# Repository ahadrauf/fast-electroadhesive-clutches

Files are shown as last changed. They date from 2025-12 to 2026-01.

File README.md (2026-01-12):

# Optimizing Electroadhesive Clutches for Sub-Millisecond Response Times

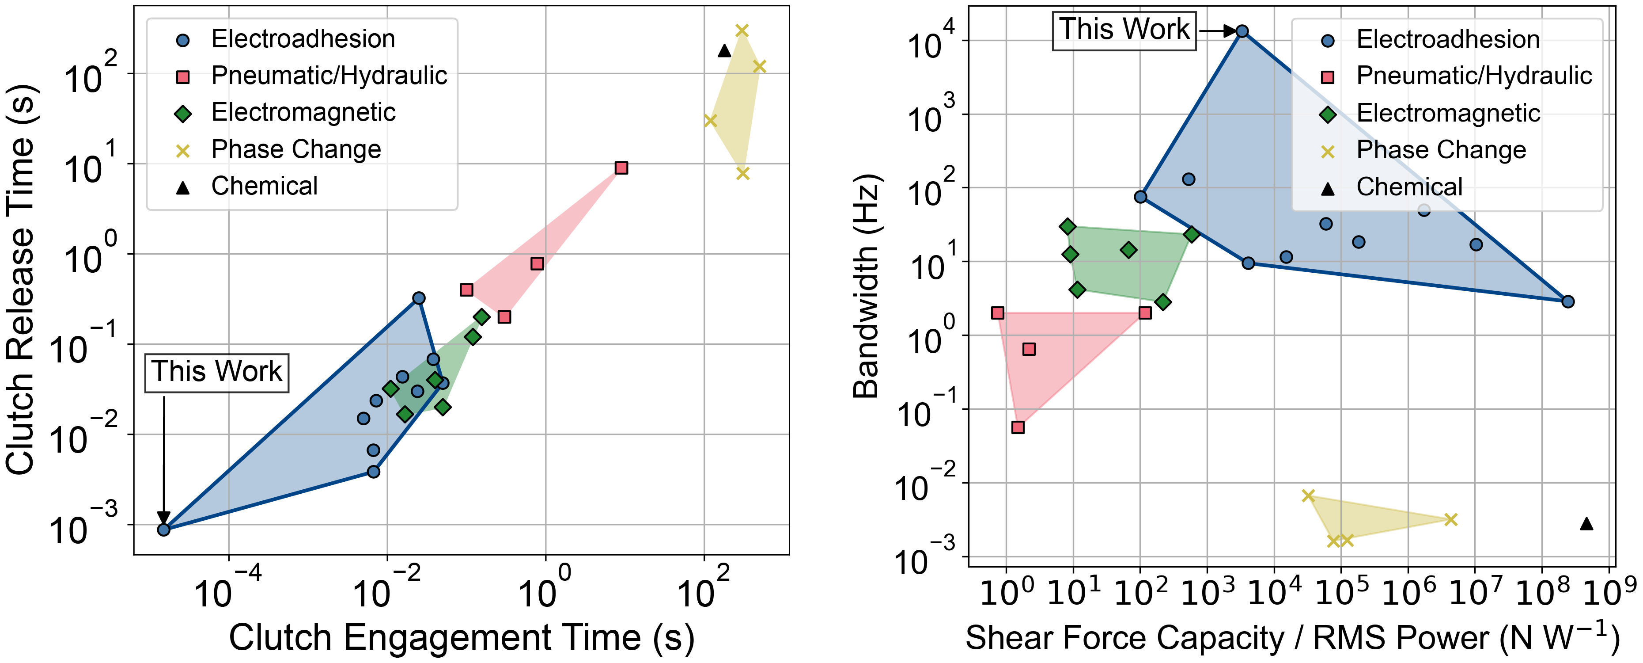
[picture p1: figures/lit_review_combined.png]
This study presents fast, electrically controllable electroadhesive clutches that offer over 10x faster engagement, release, and dynamic bandwidth compared to prior work and other clutch technologies.


Robots can use fast, controllable clutches for dynamic load bearing and programmable stiffness. Electroadhesion (EA) is a technology that offers these capabilities in an ultra-compact and flexible form factor, but its inconsistent dynamics limit real-world use.

To address this uncertainty, we built an analytical electromechanical dynamics model for electroadhesion, factoring in contact mechanics between the dielectric and substrate, polarization dynamics, and the drive circuitry’s rise and fall times. Dual optimization over both the electrical and contact mechanics allows us to improve clutch dynamics while maintaining high force output. The fastest clutches in our study can repeatably:
 * Engage in <15 μs (10x faster than prior work)
 * Release in <1 ms (17x faster than prior work)
 * Bandwidth >10 kHz (10x higher than prior work)
 * Recover after slip in <4 ms (roughly 5x faster than prior work)

In the main paper (open access link [here](https://arxiv.org/abs/2412.16803), journal link [here](https://www.sciencedirect.com/science/article/abs/pii/S235243162500094X)), we compare our model’s predictions for electroadhesive engagement and release times to experimental results across four operating and geometric design parameters with good conformity. We find that higher drive frequencies and narrower substrate aspect ratios enable significantly faster actuator response times, in particular improving release times.

We also compare our model’s predictions to broader experimental trends in prior literature, in particular explaining why larger substrate widths and lengths, lower voltages, and intermediate dielectric thicknesses result in larger release times. To our knowledge, this is the first analytical model for electroadhesion explaining these experimental trends.

## Methods (Modeling)
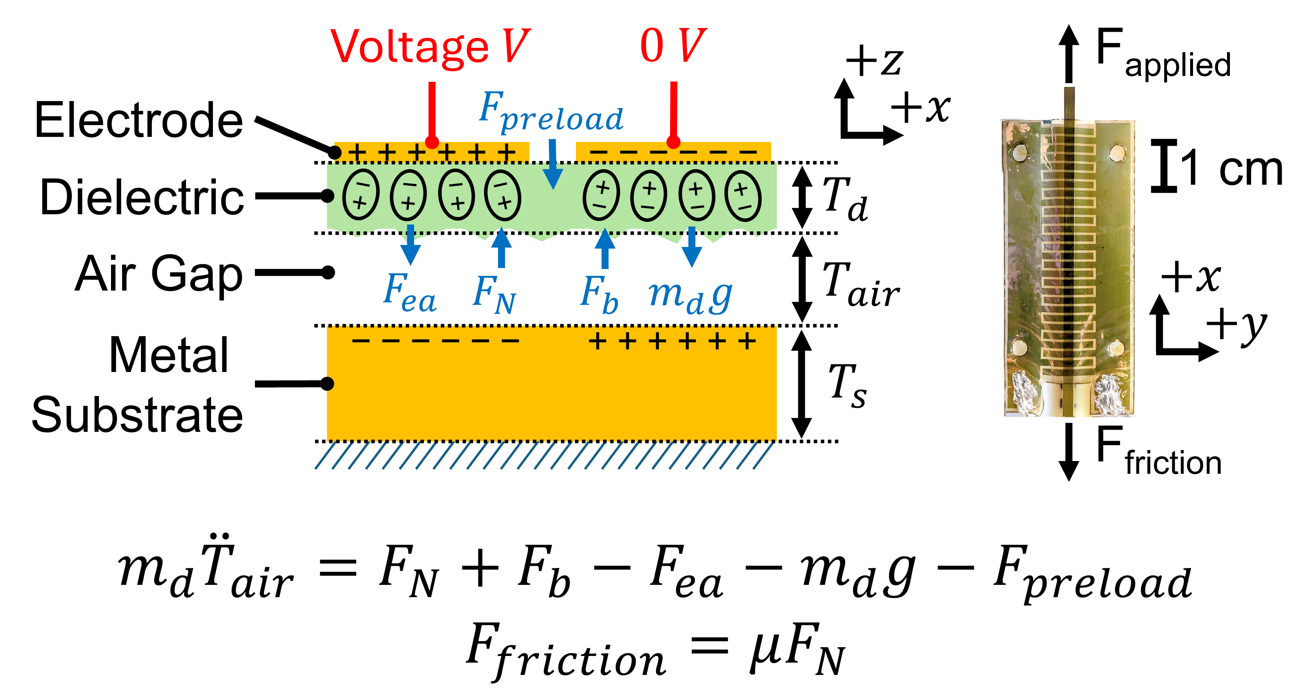
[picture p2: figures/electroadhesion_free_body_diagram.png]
Free body diagram and visualization of an electroadhesive clutch adhering to a metal substrate

Our analytical model for electroadhesion dynamics included, from left to right in the equation above, the contact mechanics force between the dielectric and substrate, squeeze film damping, the electroadhesive attractive force, the dielectric's weight, and any external applied loads.

Using our free body diagram, we simulated how these parameters affect electroadhesion’s quasistatic and dynamic performance, and we validated these simulations via both finite element analysis and experimental testing.  

## Methods (Experimental)
To measure the engagement and release times of electroadhesive clutches down to the tens of microseconds, we built a custom tensile testing setup, as shown below.

We also designed a custom high voltage DC-DC converter and shift register circuit, the schematic of which is shown below.

Experimental test setup for measuring EA shear force as the load cell on a motorized stage pushes against the substrate.

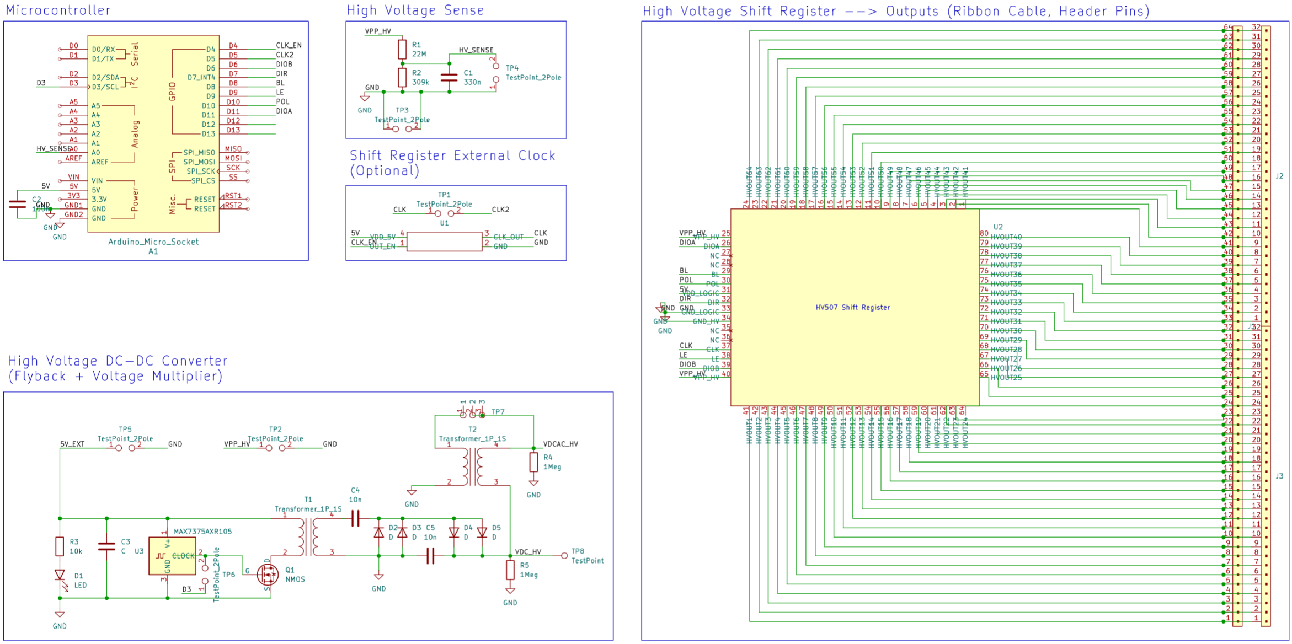
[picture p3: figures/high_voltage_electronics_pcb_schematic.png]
Schematic for the high voltage electronics, featuring a flyback transformer and voltage multiplier to produce the high voltage and a 64-channel shift register to control the electroadhesive clutch.


## Navigating This Repository
Each of the figures in the ``scripts/`` folder are named according to the paper figure they generate. The experimental data that produced these figures are stored in the ``data/`` folder (mostly comprising log files for the ~400 tensile testing experiments reported on in this paper).

The code to run a tensile test is located in ``scripts/run_tensile_test.py``. This script expects that the code in the ``teensy/`` folder has also been loaded onto both the Teensy microcontrollers controlling the tensile testing setup and the shift register PCB.

CAD files for the tensile testing setup are located in the ``cad/`` folder, and KiCAD PCB files for the Microchip HV 507 shift register and power electronics circuit are located in the ``pcb/`` folder.

## Bibliography
[1] A. M. Rauf and S. Follmer, “Modeling the dynamics of sub-millisecond electroadhesive engagement and release times,” Extreme Mechanics Letters, vol. 79, p. 102382, Sept. 2025, doi: [10.1016/j.eml.2025.102382](https://doi.org/10.1016/j.eml.2025.102382). (Open Access arXiv link [here](https://arxiv.org/abs/2412.16803))

@article{Rauf_Follmer_2025, title={Modeling the dynamics of sub-millisecond electroadhesive engagement and release times}, volume={79}, rights={All rights reserved}, ISSN={2352-4316}, DOI={10.1016/j.eml.2025.102382}, abstractNote={Electroadhesive clutches are electrically controllable switchable adhesives commonly used in soft robots and haptic user interfaces. They can form strong bonds to a wide variety of surfaces at low power consumption. However, electroadhesive clutches in the literature engage to and release from substrates several orders of magnitude slower than a traditional electrostatic model would predict. Large release times, in particular, can limit electroadhesion’s usefulness in high-bandwidth applications. We develop a novel electromechanical model for electroadhesion, factoring in polarization dynamics, the drive circuitry’s rise and fall times, and contact mechanics between the dielectric and substrate. We show in simulation and experimentally how different design parameters affect the engagement and release times of centimeter-scale electroadhesive clutches to metallic substrates, and we find that the model accurately captures the magnitude and trends of our experimental results. In particular, we find that higher drive frequencies, narrower substrate aspect ratios, and faster drive circuitry output stages enable significantly faster release times. The fastest clutches have engagement times less than 15μs and release times less than 875μs, which are 10× and 17.1× faster, respectively, than the best times found in prior literature on centimeter-scale electroadhesive clutches.}, journal={Extreme Mechanics Letters}, author={Rauf, Ahad M. and Follmer, Sean}, year={2025}, month=sept, pages={102382} }

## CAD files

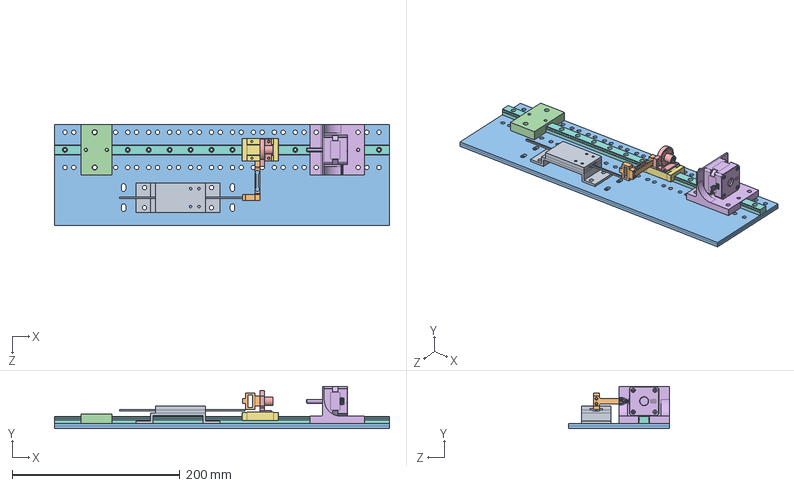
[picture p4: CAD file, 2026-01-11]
cad/tensile_testing_setup.SLDASM
400.0 x 50.3 x 120.0 mm
Linear Guide Rail LML9B
Linear Guide Block LML9B
20240705_msd_bts_nema14_mount
20240705_msd_bts_leadscrew_linearslide_adapter
20240705_msd_bts_leadscrew_fixedbearing_mount
20240705_msd_bts_baseplate
20240705_500g_load_cell
20240706_msd_bts_ea_brake_mount_40mm

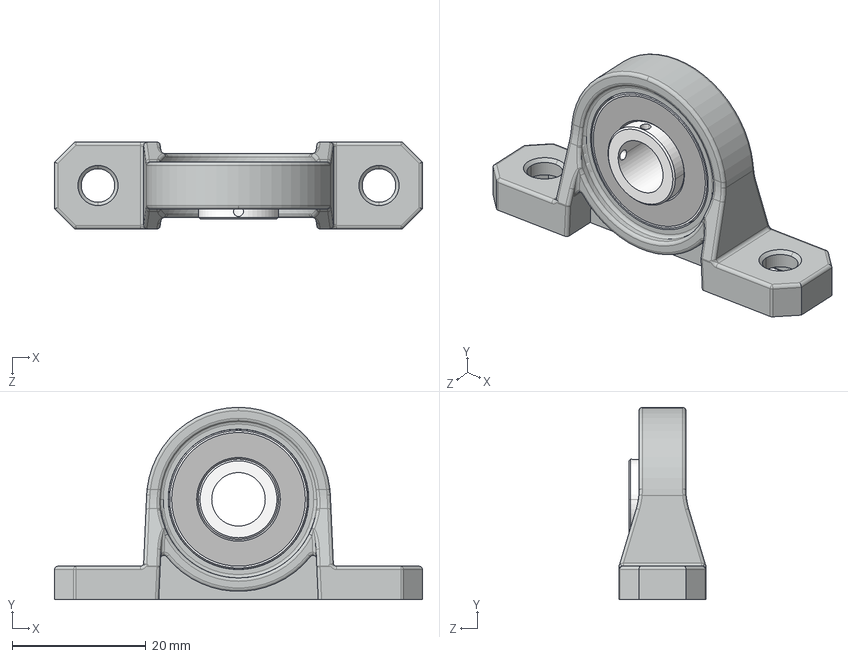
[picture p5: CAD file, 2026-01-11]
cad/pillow_block_8mm.STEP
55.0 x 28.8 x 13.0 mm

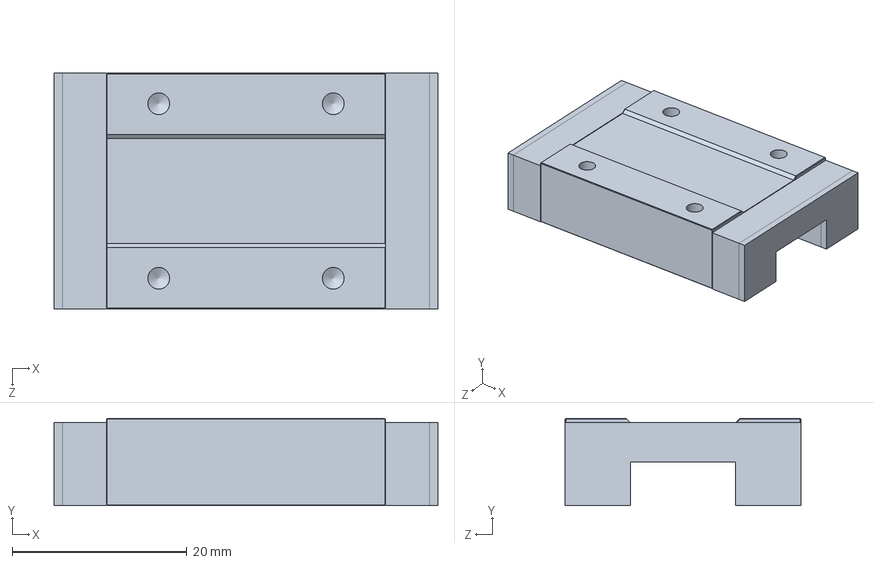
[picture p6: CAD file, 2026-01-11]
cad/Linear Guide Block LML9B.SLDPRT
44.0 x 10.0 x 27.0 mm

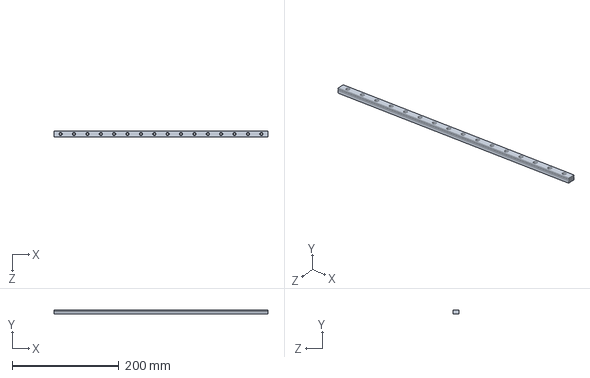
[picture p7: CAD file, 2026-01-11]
cad/Linear Guide Rail LML9B.SLDPRT
400.0 x 8.00 x 12.0 mm

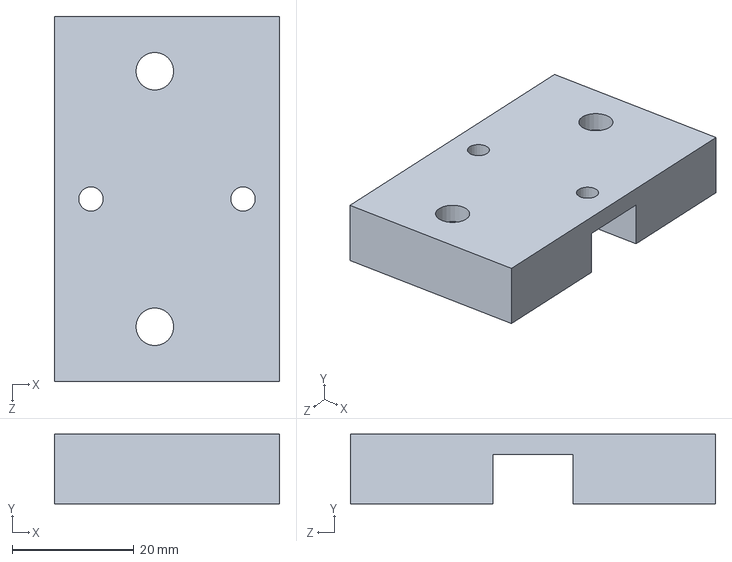
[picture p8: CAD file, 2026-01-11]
cad/20240705_msd_bts_leadscrew_fixedbearing_mount.SLDPRT
37.0 x 11.5 x 60.0 mm

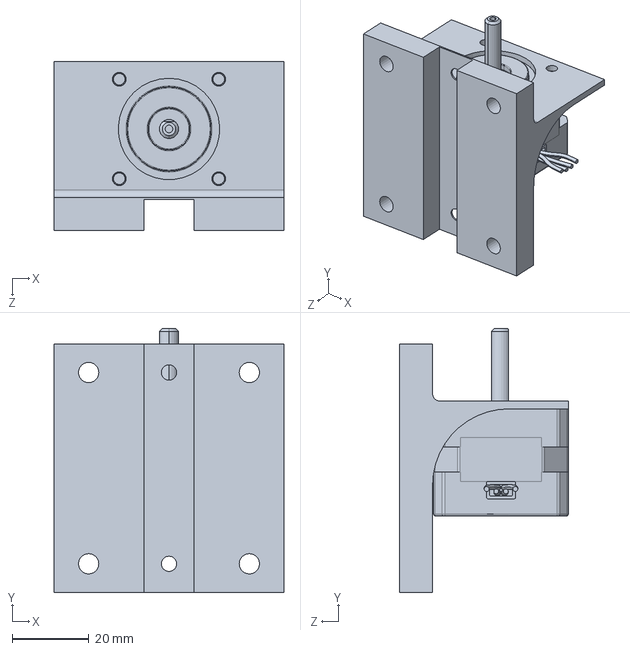
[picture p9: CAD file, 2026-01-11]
cad/20240705_msd_bts_nema14_mount.SLDPRT
60.0 x 69.0 x 44.1 mm

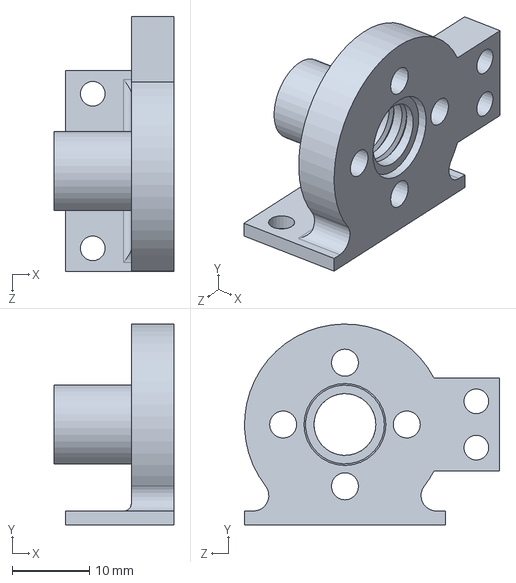
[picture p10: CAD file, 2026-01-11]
cad/20240705_msd_bts_leadscrew_linearslide_adapter.SLDPRT
15.5 x 26.0 x 33.0 mm

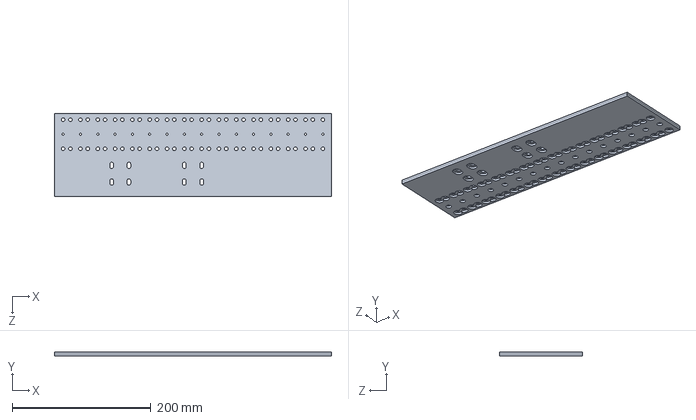
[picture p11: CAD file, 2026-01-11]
cad/20240705_msd_bts_baseplate.SLDPRT
400.0 x 6.16 x 120.0 mm

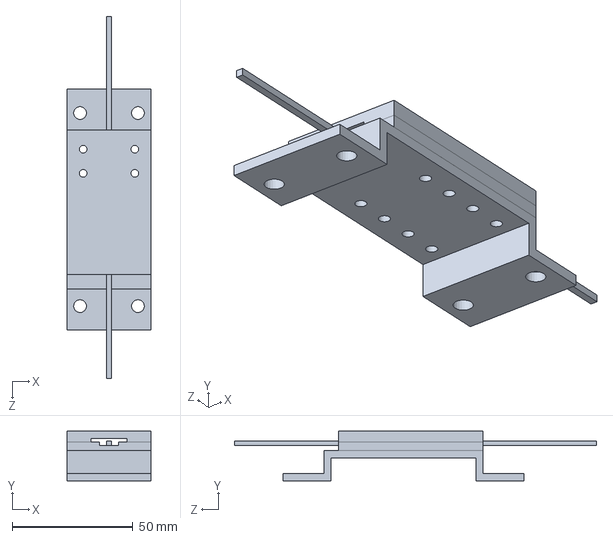
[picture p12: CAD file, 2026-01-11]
cad/20240706_msd_bts_ea_brake_mount_40mm.SLDPRT
35.0 x 20.7 x 150.0 mm

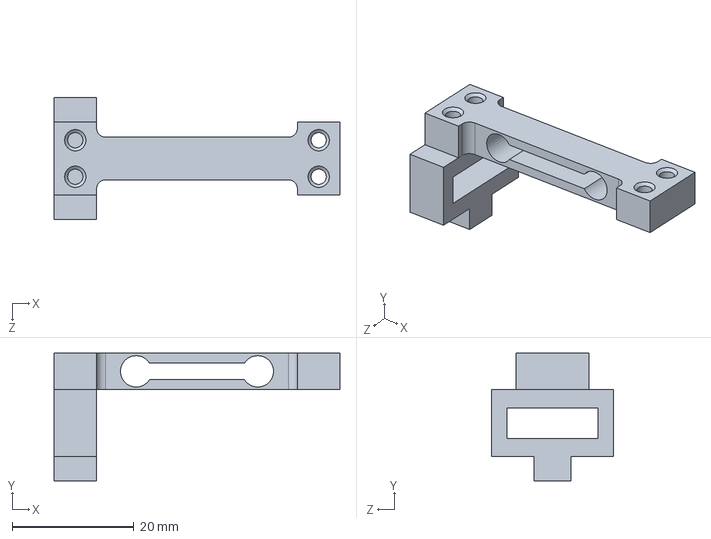
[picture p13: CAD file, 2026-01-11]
cad/20240705_500g_load_cell.SLDPRT
47.0 x 21.0 x 20.0 mm

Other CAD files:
cad/pillow_block_8mm.SLDPRT

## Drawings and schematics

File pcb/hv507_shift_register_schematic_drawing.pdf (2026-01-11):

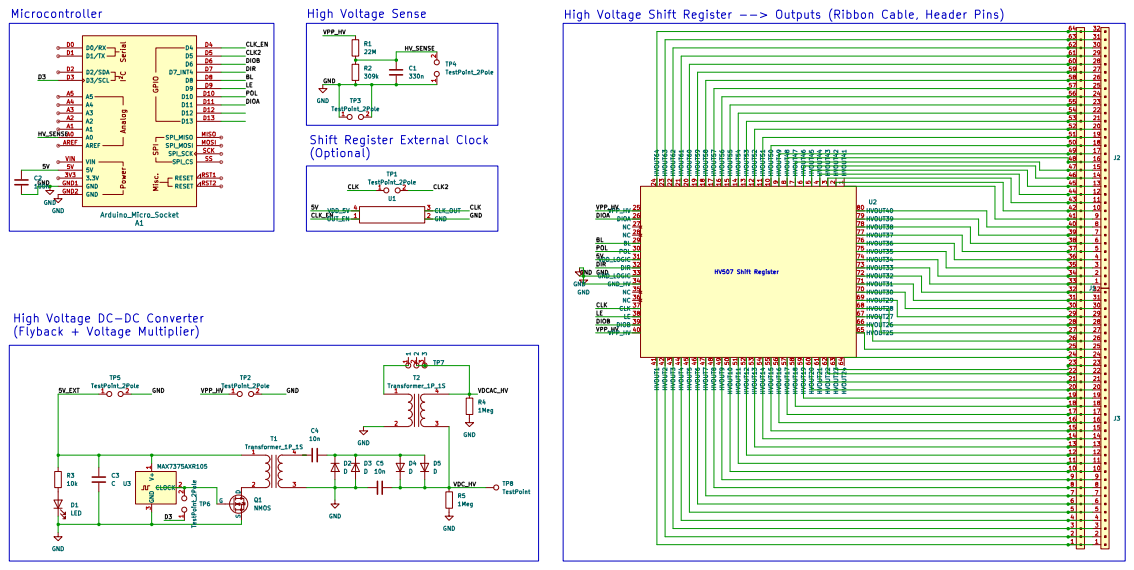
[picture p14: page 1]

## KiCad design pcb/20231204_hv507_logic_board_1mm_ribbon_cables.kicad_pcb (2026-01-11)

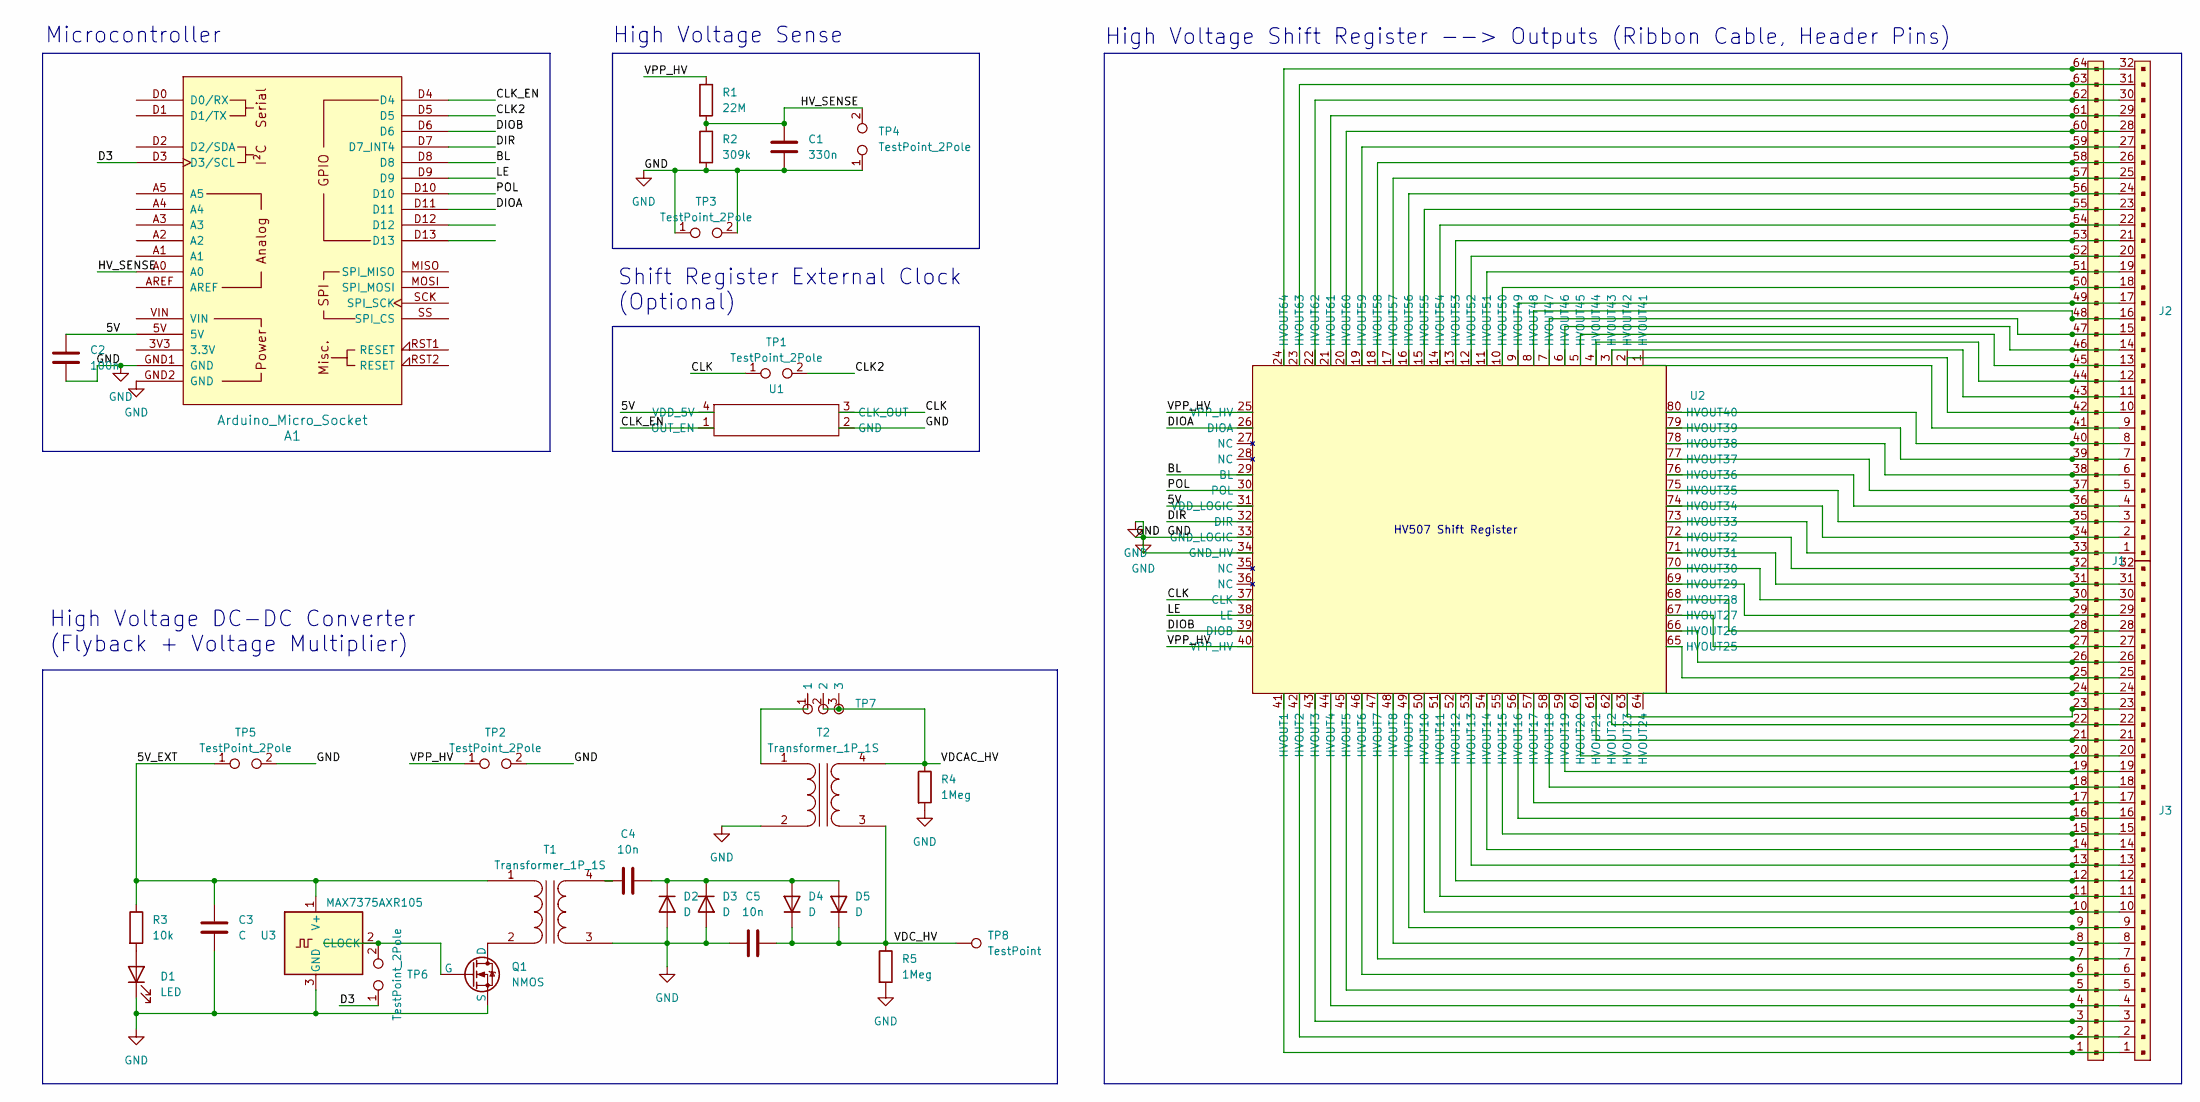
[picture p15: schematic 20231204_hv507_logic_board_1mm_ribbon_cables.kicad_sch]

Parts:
A1: Arduino_Micro_Socket; Arduino_Micro_Socket_ProbeRow
C1: 330n; C_0603_1608Metric_Pad1.08x0.95mm_HandSolder
C2: 100n; C_0603_1608Metric_Pad1.08x0.95mm_HandSolder
C3: C; C_0603_1608Metric_Pad1.08x0.95mm_HandSolder
C4, C5: 10n; C_0603_1608Metric_Pad1.08x0.95mm_HandSolder
D1: LED; C_0603_1608Metric_Pad1.08x0.95mm_HandSolder
D2, D4: D; TO-220-2_Vertical
D3, D5: D; D_SOD-523
J1: PinHeader_32x2_P2.54mm_Vertical2
J2, J3: CF25321D0R0-10-NH
Q1: NMOS; SOT-883
R1: 22M; R_0805_2012Metric_Pad1.20x1.40mm_HandSolder
R2: 309k; R_0805_2012Metric_Pad1.20x1.40mm_HandSolder
R3: 10k; R_0805_2012Metric_Pad1.20x1.40mm_HandSolder
R4, R5: 1Meg; R_0805_2012Metric_Pad1.20x1.40mm_HandSolder
T1: Transformer_1P_1S; UA7868-AE Coupled Inductor
T2: Transformer_1P_1S; LPD5030V 1-1 Coupled Inductor
TP1, TP2, TP3, TP4, TP5, TP6: TestPoint_2Pole; PinHeader_1x02_P2.54mm_Vertical
TP7: PinHeader_1x03_P2.54mm_Vertical
TP8: TestPoint; PinHeader_1x01_P2.54mm_Vertical
U1: SMD-4_3.2x2.5
U2: PQFP-80_14x20mm_P0.8mm
U3: MAX7375AXR105; SOT-323_SC-70

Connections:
/5V: A1.5V, C2.1, U1.4 (VDD_5V), U2.31 (VDD_LOGIC)
/5V_EXT: C3.2, R3.1, T1.1 (AA), TP5.1, U3.1 (V+)
/BL: A1.D8, U2.29 (BL)
/CLK: TP1.1, U1.3 (CLK_OUT), U2.37 (CLK)
/CLK2: A1.D5, TP1.2
/CLK_EN: A1.D4, U1.1 (OUT_EN)
/D3: A1.D3 (D3/SCL), TP6.1
/DIOA: A1.D11, U2.26 (DIOA)
/DIOB: A1.D6, U2.39 (DIOB)
/DIR: A1.D7 (D7_INT4), U2.32 (DIR)
/HV_SENSE: A1.A0, C1.1, R1.2, R2.1, TP4.2
/LE: A1.D9, U2.38 (LE)
/POL: A1.D10, U2.30 (POL)
/VDCAC_HV: R4.1, T2.4 (SB), TP7.2, TP7.3
/VDC_HV: C5.2, D4.1 (K), D5.1 (K), R5.1, T2.3 (SA), TP8.1
/VPP_HV: R1.1, TP2.1, U2.25 (VPP_HV), U2.40 (VPP_HV)
GND: A1.GND1 (GND), A1.GND2 (GND), C1.2, C2.2, C3.1, C5.1, D1.1 (K), D2.2 (A), D3.2 (A), Q1.3 (S), R2.2, R4.2, R5.2, T1.3 (SA), T2.2 (AB), TP2.2, TP3.1, TP3.2, TP4.1, TP5.2, U1.2 (GND), U2.33 (GND_LOGIC), U2.34 (GND_HV), U3.3 (GND)
unnamed: D1.2 (A), R3.2
unnamed: C4.2, D2.1 (K), D3.1 (K), D4.2 (A), D5.2 (A)
unnamed: Q1.1 (D), T1.2 (AB)
unnamed: Q1.2 (G), TP6.2, U3.2 (CLOCK)
unnamed: C4.1, T1.4 (SB)
unnamed: T2.1 (AA), TP7.1
unnamed: J1.1, J3.1, U2.41 (HVOUT1)
unnamed: J1.2, J3.2, U2.42 (HVOUT2)
unnamed: J1.3, J3.3, U2.43 (HVOUT3)
unnamed: J1.4, J3.4, U2.44 (HVOUT4)
unnamed: J1.5, J3.5, U2.45 (HVOUT5)
unnamed: J1.6, J3.6, U2.46 (HVOUT6)
unnamed: J1.7, J3.7, U2.47 (HVOUT7)
unnamed: J1.8, J3.8, U2.48 (HVOUT8)
unnamed: J1.9, J3.9, U2.49 (HVOUT9)
unnamed: J1.10, J3.10, U2.50 (HVOUT10)
unnamed: J1.11, J3.11, U2.51 (HVOUT11)
unnamed: J1.12, J3.12, U2.52 (HVOUT12)
unnamed: J1.13, J3.13, U2.53 (HVOUT13)
unnamed: J1.14, J3.14, U2.54 (HVOUT14)
unnamed: J1.15, J3.15, U2.55 (HVOUT15)
unnamed: J1.16, J3.16, U2.56 (HVOUT16)
unnamed: J1.17, J3.17, U2.57 (HVOUT17)
unnamed: J1.18, J3.18, U2.58 (HVOUT18)
unnamed: J1.19, J3.19, U2.59 (HVOUT19)
unnamed: J1.20, J3.20, U2.60 (HVOUT20)
unnamed: J1.21, J3.21, U2.61 (HVOUT21)
unnamed: J1.22, J3.22, U2.62 (HVOUT22)
unnamed: J1.23, J3.23, U2.63 (HVOUT23)
unnamed: J1.24, J3.24, U2.64 (HVOUT24)
unnamed: J1.25, J3.25, U2.65 (HVOUT25)
unnamed: J1.26, J3.26, U2.66 (HVOUT26)
unnamed: J1.27, J3.27, U2.67 (HVOUT27)
unnamed: J1.28, J3.28, U2.68 (HVOUT28)
unnamed: J1.29, J3.29, U2.69 (HVOUT29)
unnamed: J1.30, J3.30, U2.70 (HVOUT30)
unnamed: J1.31, J3.31, U2.71 (HVOUT31)
unnamed: J1.32, J3.32, U2.72 (HVOUT32)
unnamed: J1.33, J2.1, U2.73 (HVOUT33)
unnamed: J1.34, J2.2, U2.74 (HVOUT34)
unnamed: J1.35, J2.3, U2.75 (HVOUT35)
unnamed: J1.36, J2.4, U2.76 (HVOUT36)
unnamed: J1.37, J2.5, U2.77 (HVOUT37)
unnamed: J1.38, J2.6, U2.78 (HVOUT38)
unnamed: J1.39, J2.7, U2.79 (HVOUT39)
unnamed: J1.40, J2.8, U2.80 (HVOUT40)
unnamed: J1.41, J2.9, U2.1 (HVOUT41)
unnamed: J1.42, J2.10, U2.2 (HVOUT42)
unnamed: J1.43, J2.11, U2.3 (HVOUT43)
unnamed: J1.44, J2.12, U2.4 (HVOUT44)
unnamed: J1.45, J2.13, U2.5 (HVOUT45)
unnamed: J1.46, J2.14, U2.6 (HVOUT46)
unnamed: J1.47, J2.15, U2.7 (HVOUT47)
unnamed: J1.48, J2.16, U2.8 (HVOUT48)
unnamed: J1.49, J2.17, U2.9 (HVOUT49)
unnamed: J1.50, J2.18, U2.10 (HVOUT50)
unnamed: J1.51, J2.19, U2.11 (HVOUT51)
unnamed: J1.52, J2.20, U2.12 (HVOUT52)
unnamed: J1.53, J2.21, U2.13 (HVOUT53)
unnamed: J1.54, J2.22, U2.14 (HVOUT54)
unnamed: J1.55, J2.23, U2.15 (HVOUT55)
unnamed: J1.56, J2.24, U2.16 (HVOUT56)
unnamed: J1.57, J2.25, U2.17 (HVOUT57)
unnamed: J1.58, J2.26, U2.18 (HVOUT58)
unnamed: J1.59, J2.27, U2.19 (HVOUT59)
unnamed: J1.60, J2.28, U2.20 (HVOUT60)
unnamed: J1.61, J2.29, U2.21 (HVOUT61)
unnamed: J1.62, J2.30, U2.22 (HVOUT62)
unnamed: J1.63, J2.31, U2.23 (HVOUT63)
unnamed: J1.64, J2.32, U2.24 (HVOUT64)

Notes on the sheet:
HV507 Shift Register
High Voltage DC-DC Converter (Flyback + Voltage Multiplier)
High Voltage Shift Register --> Outputs (Ribbon Cable, Header Pins)
Shift Register External Clock (Optional)
Microcontroller
High Voltage Sense

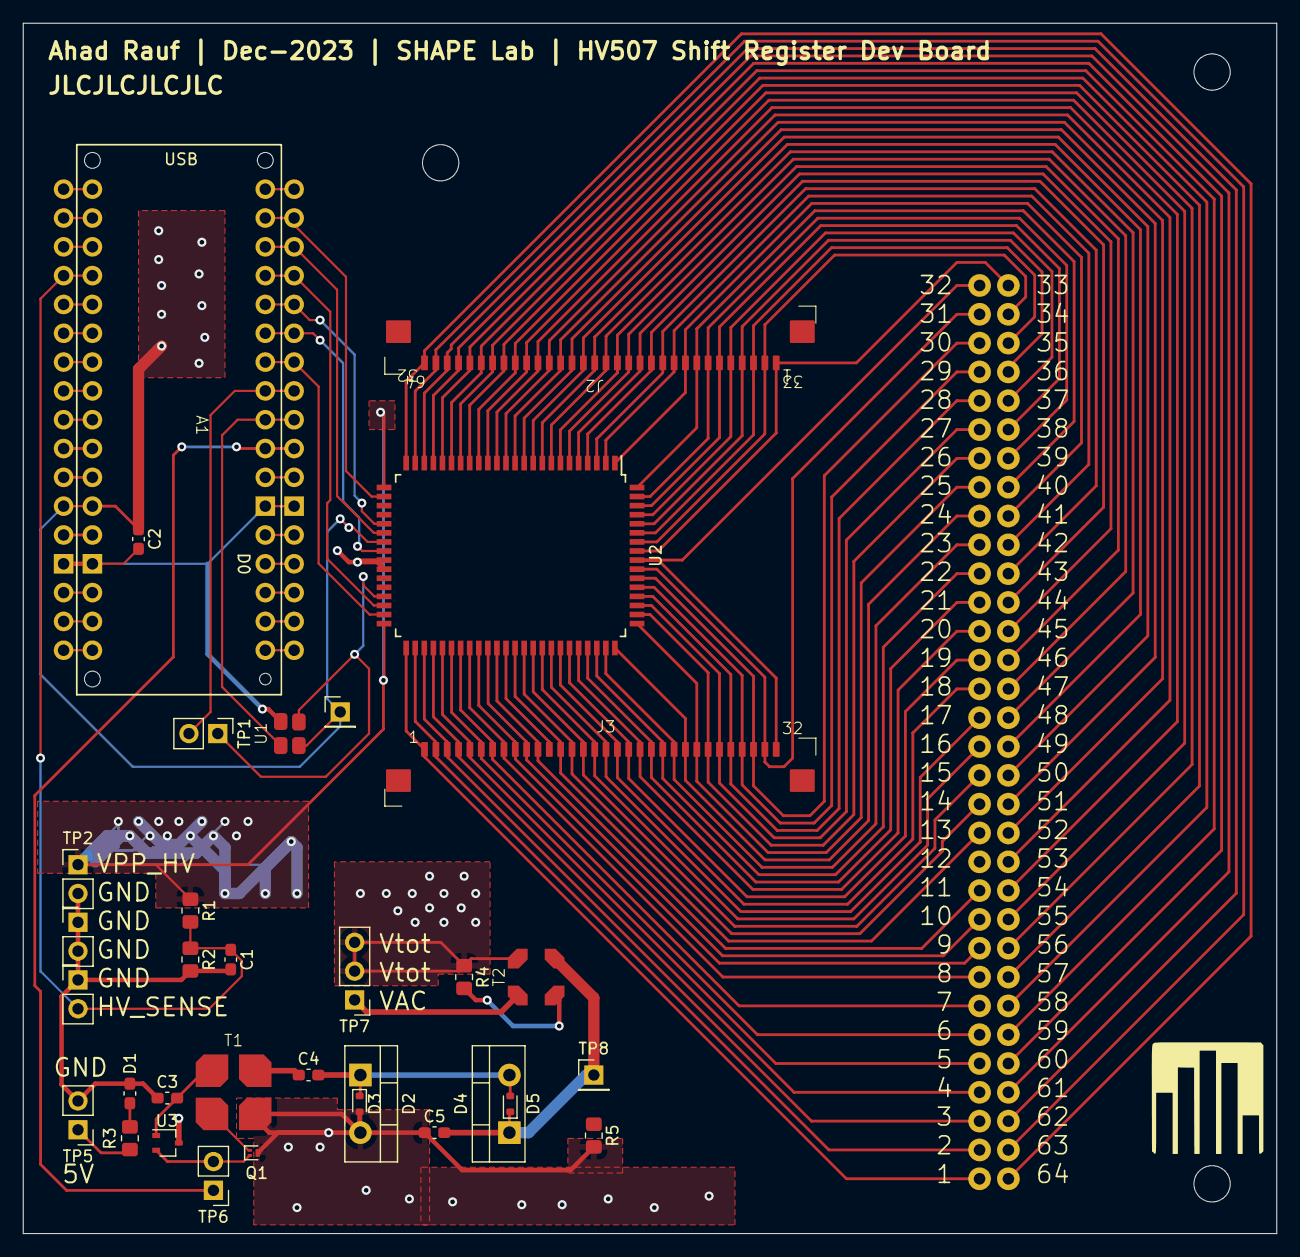
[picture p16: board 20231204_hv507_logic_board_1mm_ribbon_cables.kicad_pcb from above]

Board: 2 copper layers, 110.5 x 106.7 mm, 33 parts (1 on the bottom side), 87 nets.

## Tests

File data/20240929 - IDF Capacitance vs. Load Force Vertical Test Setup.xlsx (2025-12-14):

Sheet: w=2 (20240929_234547707)
Force (N) | Capacitance (pF) | Gap (um)
0.0015 | 12.8 | 13.90417966 |  |  | w | 0.002
0.003 | 13.7 | 12.94989048 |  |  | L | 0.06
0.004 | 14.7 | 12.02661751 |  |  | Aspect Ratio | 0.03333333333
0.01 | 16.7 | 10.5117864 |  |  | Thickness | 2.8e-05
0.098 | 22.5 | 7.641686403
0.361 | 25.3 | 6.72710363
0.732 | 29.4 | 5.702197644
1.136 | 31.9 | 5.206553454
1.523 | 33.5 | 4.928164168
2.111 | 34.3 | 4.798709092
2.64 | 35.7 | 4.58612355
3.11 | 36.2 | 4.514185072 | 27.3
3.53 | 37 | 4.403127617
4.01 | 37.2 | 4.376109608 | 4.9 | 26.8
4.63 | 37.7 | 4.309818735
5.17 | 38.4 | 4.219911738 | -7.79686506 | 38.12841103
5.86 | 39.1 | 4.133223918
6.5 | 39.7 | 4.061353195
7.14 | 40.4 | 3.980202136
7.67 | 40.9 | 3.923937779
8.26 | 41.4 | 3.869032465 | Expected Slope
 |  |  | 0.3296703297
 |  |  | 3.882709565 | 0.0235551047
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

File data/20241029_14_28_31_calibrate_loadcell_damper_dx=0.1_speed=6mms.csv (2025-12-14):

Time | Load Cell | Moving Forward
879.0 | -0.00705895 | 0.0
927.0 | -0.00517961 | 0.0
1005.0 | -0.00888745 | 0.0
1083.0 | -0.00157329 | 0.0
1161.0 | 0.00863598 | 0.0
1239.0 | -0.00055744 | 0.0
1317.0 | -0.01015734 | 0.0
1396.0 | -0.00228434 | 0.0
1474.0 | -0.02874745 | 0.0
1552.0 | -0.00467168 | 0.0
1630.0 | 0.00939787 | 0.0
1708.0 | -0.01168111 | 0.0
1786.0 | 0.00111878 | 0.0
1864.0 | -0.00020188 | 0.0
1942.0 | 0.00157586 | 0.0
2021.0 | -0.008278 | 0.0
2099.0 | -0.00248762 | 0.0
2177.0 | 0.0036584 | 0.0
2255.0 | 0.00492814 | 0.0
2333.0 | -0.01442394 | 0.0
2411.0 | -0.00690651 | 0.0
2489.0 | -0.00228434 | 0.0
2567.0 | 0.00208379 | 0.0
2645.0 | -0.02387132 | 0.0
2724.0 | 0.00629956 | 0.0
2802.0 | -0.00131933 | 0.0
2880.0 | 0.00137259 | 0.0
2958.0 | -0.00507801 | 0.0
3036.0 | 0.01554389 | 0.0
3114.0 | -0.00431612 | 0.0
3192.0 | -0.0104113 | 0.0
3270.0 | 0.01066776 | 0.0
3349.0 | 0.02361993 | 0.0
3427.0 | 0.00381069 | 0.0
3505.0 | 0.00254088 | 0.0
3583.0 | 0.00553774 | 0.0
3661.0 | 0.02473731 | 0.0
3739.0 | 0.00218531 | 0.0
3817.0 | 0.00797569 | 0.0
3895.0 | -0.00837952 | 0.0
3974.0 | 0.00289644 | 0.0
4052.0 | -0.00106529 | 0.0
4130.0 | 0.00670596 | 0.0
4208.0 | -0.01924916 | 0.0
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

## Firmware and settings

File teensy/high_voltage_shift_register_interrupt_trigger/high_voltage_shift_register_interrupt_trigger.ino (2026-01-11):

/***
Teensy 3.6 code for controlling the Microchip HV507 high voltage shift register

When the Teensy receives a trigger, it starts toggling the HV507 at a pre-defined bipolar
    square wave frequency. The code accepts two types of triggers: either the other Teensy
    triggers it by connecting the two Teensy's ground pins and linking the other Teensy's
    INTERRUPT_PIN to this Teensy's BUTTON_IN_PIN, or a push button can be connected between 
    this Teensy's BUTTON_IN_PIN and BUTTON_OUT_PIN (for other applications).
***/

#include "hv507.h"

const int PIN_CLK_EN = 24;
const int PIN_CLK = 25;
const int PIN_DIOB = 26;
const int PIN_DIR = 27;
const int PIN_BL = 28;
const int PIN_LE = 29;
const int PIN_POL = 30;
const int PIN_DIOA = 31;

const int LED_PIN = 13;
const int BUTTON_IN_PIN = 34;
const int BUTTON_OUT_PIN = 33;
const float FREQUENCY = 100;  // bipolar square wave drive frequency
const int DELAY = 1e6 / FREQUENCY / 2;
volatile int currIdx = 0;
bool forward = true;
volatile bool enabled = false;
volatile bool voltage_on_electrode1 = false;

HV507 hv507;
IntervalTimer timerBipolarSquareWave;

void setup() {
  pinMode(PIN_DIOB, INPUT);
  pinMode(BUTTON_OUT_PIN, OUTPUT);
  hv507.init(PIN_CLK, PIN_LE, PIN_DIOA, PIN_POL, PIN_BL, PIN_DIR);
  delay(100);
  hv507.loadArrayToRegister(0, 0, 0, 0);
  hv507.loadRegisterToOutput();
  pinMode(LED_PIN, OUTPUT);
  pinMode(BUTTON_IN_PIN, INPUT);
  digitalWrite(BUTTON_OUT_PIN, LOW);
  attachInterrupt(digitalPinToInterrupt(BUTTON_IN_PIN), hv507Toggle, CHANGE);
}

void loop() { }

void hv507Toggle() {
  if (digitalRead(BUTTON_IN_PIN) == HIGH) {
    timerBipolarSquareWave.end();
    digitalWrite(LED_PIN, HIGH);
    hv507.loadArrayToRegister(0x0100, 0x0000, 0x0000, 0x0000);
    hv507.loadRegisterToOutput();
    voltage_on_electrode1 = true;
    enabled = true;
    digitalWrite(BUTTON_OUT_PIN, HIGH);
    timerBipolarSquareWave.begin(hv507InvertOutputs, DELAY); // update time (us)
  } else {
    digitalWrite(LED_PIN, LOW);

    // Comment out for frequencies other than 0.1 Hz (so I'm logging voltages from the proper electrode)
    // timerBipolarSquareWave.end();
    // hv507.loadArrayToRegister(0x0000, 0x0000, 0x0000, 0x0000);
    // hv507.loadRegisterToOutput();
    // digitalWrite(BUTTON_OUT_PIN, LOW);
    // voltage_on_electrode1 = false;

    enabled = false;
  }
}

void hv507InvertOutputs() {
  if (voltage_on_electrode1 && enabled) {
    hv507.loadArrayToRegister(0x0000, 0x0000, 0x0000, 0x0080); // corresponds to pin 56 (56-48=8 --> plug 1000,0000 into https://www.rapidtables.com/convert/number/hex-to-binary.html?x=80)
    hv507.loadRegisterToOutput();
    voltage_on_electrode1 = false;
  } else if (!voltage_on_electrode1) {
    hv507.loadArrayToRegister(0x0100, 0x0000, 0x0000, 0x0000); // corresponds to pin 9
    hv507.loadRegisterToOutput();
    voltage_on_electrode1 = true;
  } else { // !voltage_on_electrode1 && !enabled (interrupt triggered to end voltage)
    hv507.loadArrayToRegister(0x0000, 0x0000, 0x0000, 0x0000); 
    hv507.loadRegisterToOutput();
    digitalWrite(BUTTON_OUT_PIN, LOW);
    voltage_on_electrode1 = false;
    timerBipolarSquareWave.end();
  }
}

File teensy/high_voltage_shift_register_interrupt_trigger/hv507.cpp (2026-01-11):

#include "hv507.h"

void HV507::init(int8_t clockPin, int8_t latchPin, int8_t dataPin, int8_t polarityPin, int8_t blankingPin, int8_t directionPin)
{
  _clockPin = clockPin;
  _latchPin = latchPin;
  _dataPin = dataPin;
  _polarityPin = polarityPin;
  _blankingPin = blankingPin;
  _directionPin = directionPin;

  pinMode(_clockPin, OUTPUT);
  pinMode(_latchPin, OUTPUT);
  pinMode(_dataPin, OUTPUT);
  pinMode(_polarityPin, OUTPUT);
  pinMode(_blankingPin, OUTPUT);
  pinMode(_directionPin, OUTPUT);
  digitalWrite(_clockPin, LOW);  // don't assume what _clockPin is after each function, usu. HIGH though
  digitalWrite(_latchPin, LOW);  // _latchPin is LOW after every function
  digitalWrite(_dataPin, LOW);
  digitalWrite(_polarityPin, HIGH);  // _polarityPin is HIGH after each function
  digitalWrite(_blankingPin, HIGH);  // _blankingPin is HIGH after each function
  digitalWrite(_directionPin, LOW);  // LOW if dataPin connected to DIOA, HIGH if connected to DIOB
  
  _isInitialized = true;
  _invertedOutput = false;
}

void HV507::loadBitToRegister(uint8_t data)
{
	//digitalWrite(_latchPin, LOW);
  digitalWrite(_clockPin, LOW);
  digitalWrite(_dataPin, data);
  digitalWrite(_clockPin, HIGH); // Set clock pin low ready for a rising edge
}

void HV507::loadByteToRegister(uint8_t data)  // bits 7...0 = HVOUT 7...0
{
	if (_invertedOutput) { invertOutputs(); }
    for (int i = 0; i <= 7; i++)
    {
      digitalWrite(_clockPin, LOW);
		  digitalWrite(_dataPin, data & (1 << i));
      digitalWrite(_clockPin, HIGH);
    }
}

// data1 = HVOUT 0...15, data2 = HVOUT 16...31, data3 = HVOUT 32...45, data4 = HVOUT 46...63
void HV507::loadArrayToRegister(uint16_t data1, uint16_t data2, uint16_t data3, uint16_t data4)
{
	if (_invertedOutput) { invertOutputs(); }
  for (int i = 0; i <= 15; i++) {
    digitalWrite(_clockPin, LOW);
    if (data1 & (1 << i)) {
      digitalWrite(_dataPin, HIGH);
    } else {
      digitalWrite(_dataPin, LOW);
    }
    digitalWrite(_clockPin, HIGH);
  }
  for (int i = 0; i <= 15; i++) {
    digitalWrite(_clockPin, LOW);
    if (data2 & (1 << i)) {
      digitalWrite(_dataPin, HIGH);
    } else {
      digitalWrite(_dataPin, LOW);
    }
    digitalWrite(_clockPin, HIGH);
  }
  for (int i = 0; i <= 15; i++) {
    digitalWrite(_clockPin, LOW);
    if (data3 & (1 << i)) {
      digitalWrite(_dataPin, HIGH);
    } else {
      digitalWrite(_dataPin, LOW);
    }
    digitalWrite(_clockPin, HIGH);
  }
  for (int i = 0; i <= 15; i++) {
    digitalWrite(_clockPin, LOW);
    if (data4 & (1 << i)) {
      digitalWrite(_dataPin, HIGH);
    } else {
      digitalWrite(_dataPin, LOW);
    }
    digitalWrite(_clockPin, HIGH);
  }
}

// data1 = HVOUT 0...15, data2 = HVOUT 16...31, data3 = HVOUT 32...45, data4 = HVOUT 46...63
void HV507::loadArrayDirectlyToOutput(uint16_t data1, uint16_t data2, uint16_t data3, uint16_t data4)
{
  digitalWrite(_latchPin, HIGH);
	loadArrayToRegister(data1, data2, data3, data4);
	digitalWrite(_latchPin, LOW);
}

// load the values in the shift register to the high-voltage output
void HV507::loadInverseRegisterToOutput()
{
	// You'll see the output start to invert initially (because this matches invertOutputs())
	// On an Arduino Micro, the _latchPin commands starts ~5us after this, so you'll see 
	// the inverse of the output occur on the output ~10us after you call this function
	// (because the latches send their data on the LE pin's falling edge)
	digitalWrite(_polarityPin, LOW);
  digitalWrite(_latchPin, HIGH);
  digitalWrite(_latchPin, LOW);
	digitalWrite(_polarityPin, HIGH);
}

void HV507::loadRegisterToOutput()
{
	if (_invertedOutput) { invertOutputs(); }
    digitalWrite(_latchPin, HIGH);
    digitalWrite(_latchPin, LOW); // LE on for ~5.2us on an Arduino Micro (seems to work well)
}


void HV507::allOutputsHigh()
{
	if (_invertedOutput) { invertOutputs(); }
  digitalWrite(_polarityPin, LOW);
	digitalWrite(_blankingPin, LOW);
  digitalWrite(_blankingPin, HIGH);
	digitalWrite(_polarityPin, HIGH);
}

void HV507::allOutputsLow()
{
	if (_invertedOutput) { invertOutputs(); }
	digitalWrite(_blankingPin, LOW);
  digitalWrite(_blankingPin, HIGH);
}

void HV507::invertOutputs()
{
	if (_invertedOutput) {
		digitalWrite(_polarityPin, HIGH);
	} else {
		digitalWrite(_polarityPin, LOW);
	}
	_invertedOutput = !_invertedOutput;
}

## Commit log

2026-01-11 updated all files
    [20231204_hv507_logic_board_1mm_ribbon_cables.kicad_pcb, 20231204_hv507_logic_board_1mm_ribbon_cables.kicad_sch, 20240705_500g_load_cell.SLDPRT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]
2026-01-11 updated pcb folder structure
    [20231204_hv507_logic_board_1mm_ribbon_cables.kicad_pcb, 20231204_hv507_logic_board_1mm_ribbon_cables.kicad_sch]
